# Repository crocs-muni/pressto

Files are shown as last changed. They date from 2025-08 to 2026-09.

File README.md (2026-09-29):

# PRESSTO
Physical Response Emulation System for Secure Testing Operations is a low-cost, fully automated, and reproducible hardware analysis platform. It enables precise and repeatable testing of devices by simulating human interaction such as button presses and screen reading without compromising cryptographic security assumptions.

**Known limits of v1** (observed on the hardware): at full reach an arm can bend, so the servo pushes the arm away instead of pressing the button; and v1 uses the SG90 in both of its versions, the 180° one and the continuous-rotation one, and the continuous-rotation servos are hard to calibrate.

<p align="center">
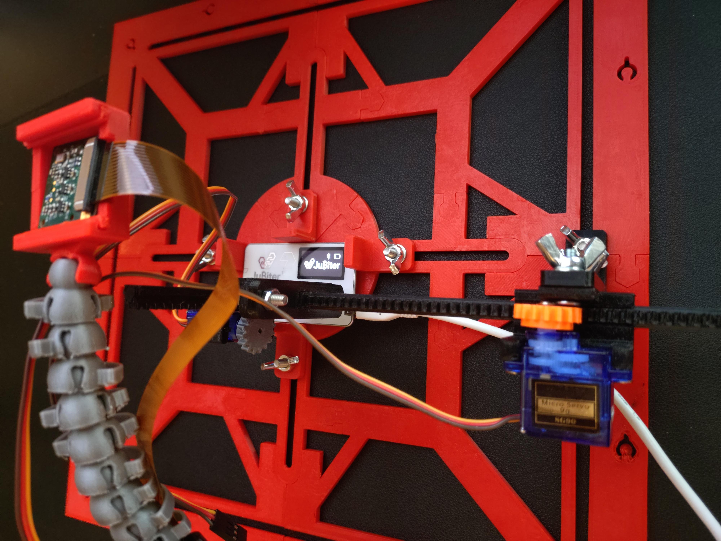
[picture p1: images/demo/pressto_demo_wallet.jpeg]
PRESSTO demo with a hardware wallet
  
  <br>
  <em>PRESSTO testing a hardware wallet</em>
</p>

## Features
- Automated physical interaction via Arduino-controlled servos
- OCR-based display capture

## Uses
- **Test physical inputs** – Consistently automate physical interaction like button presses or screen taps.  
- **Endurance testing** – Simulate hours or days of human interaction to reveal wear or intermittent faults.
- **Automated testing** – Fully automate operation of devices that can’t be driven purely by software, such as IoT appliances, hardware wallets etc.

## Where PRESSTO has been used

PRESSTO v1 was used for the study below, a large-scale security analysis of hardware wallets; so far it is PRESSTO's only published use, and this section will list further uses as they come. To cite PRESSTO, please cite this paper; its BibTeX entry follows.

[Large-Scale Security Analysis of Hardware Wallets](https://link.springer.com/chapter/10.1007/978-3-032-00633-2_21)

```bibtex
@inbook{Sorf_2025,
  title={Large-Scale Security Analysis of Hardware Wallets},
  ISBN={9783032006332},
  ISSN={1611-3349},
  url={http://dx.doi.org/10.1007/978-3-032-00633-2_21},
  DOI={10.1007/978-3-032-00633-2_21},
  booktitle={Availability, Reliability and Security},
  publisher={Springer Nature Switzerland},
  author={Šorf, Milan and Švenda, Petr and Chmielewski, Łukasz},
  year={2025},
  pages={360–377}
}
```

## Quickstart
Download the full set of models for one PRESSTO instance + printing instructions: [`quickstart.zip`](https://github.com/crocs-muni/pressto/releases/download/v1.0/quickstart.zip) (5.7 MB). The print list is also in [`stl/print.txt`](stl/print.txt).

## Bill of Materials (BOM)

This project requires a combination of 3D-printed parts, electronics, and standard mechanical fasteners. Below is the complete list of components:

### Mechanical Components

| Part | Description | DIN Spec | Quantity |
|---|---|---|---|
| M4 Hex Nuts | Standard M4 nuts for fastening | DIN 934 | Variable |
| M4 Machine Screws | M4 × 16 mm flat-head screws | DIN 965 | Variable |
| M4 Wing Nuts | Tool-free tightening, used for adjustable parts | DIN 315 | Variable |
| M4 Washers | Standard washers for load distribution | DIN 125A | Variable |

> Most joints can be assembled using a mix of these fasteners. Quantities depend on your specific configuration (number of arms, modules, etc.).

### 3D-Printed Parts

- STL files are provided in the [`stl/`](stl/) directory for immediate use.
- Original Autodesk Inventor (`.ipt`) files are also included in the [`ipt/`](ipt/) directory, allowing for easy customization and adaptation to your specific hardware or setup needs.
- Recommended print settings:
  - Material: PLA or PETG
  - Layer Height: 0.15 mm
  - Infill: 15–30% for strength
  - Supports: As needed per part
- The largest parts, measured in their STL files: `base_outer`, about 146 × 158 mm and 4 mm thick, and the racks, up to 165 mm long.

### Electronics

| Component | Notes | Quantity |
|---|---|---|
| Arduino Uno (or compatible) | For controlling servos | 1 |
| Raspberry Pi (any model with camera support) | For running OCR, camera capture, and automation scripts | 1 |
| SG90 Micro Servos | 2 per arm (e.g., one for press, one for movement) | ≥ 2 |
| Raspberry Pi Camera or USB Webcam | Used for OCR display capture | 1 |
| Power Supply | Depending on servo load | 1 |
| Display, keyboard and mouse (or remote access) | For the Raspberry Pi | — |
| USB cable | From the Arduino to the Raspberry Pi | — |
| Raspberry Pi power supply | For the Raspberry Pi (the Power Supply above is for the servos) | — |
| microSD card | For the Raspberry Pi | — |
| Camera cable | From the camera to the Raspberry Pi | — |
| Jumper wires | For the servo signal, power and ground connections | — |
| Breadboard | For the servo power and the common ground | — |
| Stylus tip (optional) | For touchscreens, grounded through a Dupont wire | — |

> The Arduino plugs into the Raspberry Pi, which drives the operation.

> Which Raspberry Pi to use depends on the use case: whether the images are processed on the Pi in real time, or only collected and sent to a stronger machine. PRESSTO v1 was tested on the Raspberry Pi Zero, 3, 4 and 5.

> "SG90" servos from one batch can be different makes, whose body dimensions differ. The holders fit both makes we measured, but cheap clones may differ, so stick with one type of servo.

> You can use a camera like the [Raspberry Pi Camera Module](https://www.raspberrypi.com/products/camera-module-3/), [Arducam](https://blog.arducam.com/raspberry-pi-multiple-cameras/) or any USB webcam (no mount is provided for a USB webcam).

### Tools

- Screwdrivers
- A spanner
- Side cutters (for the servo horn)

## Assembly Instructions

<details>
<summary><strong>Base</strong></summary>

<br>

The <strong>base</strong> forms the main support structure of the setup. It consists of 8 interlocking 3D-printed parts that slot together like a puzzle to create a rigid square frame.

### Required Parts

- 4 × [`base_inner.stl`](stl/base/base_inner.stl)
- 4 × [`base_outer.stl`](stl/base/base_outer.stl)

### Assembly Steps

1. Arrange the 4 <strong>outer</strong> parts to form the perimeter of the square.
2. Position the 4 <strong>inner</strong> parts so they form a cross-bracing pattern.
3. Slot all pieces together using the integrated puzzle joints.
4. Ensure the central circular section interlocks firmly with no gaps.  
   - No screws or adhesives are required — the snap-fit design holds everything in place.

### Visual Reference

| Description | Image |
|---|---|
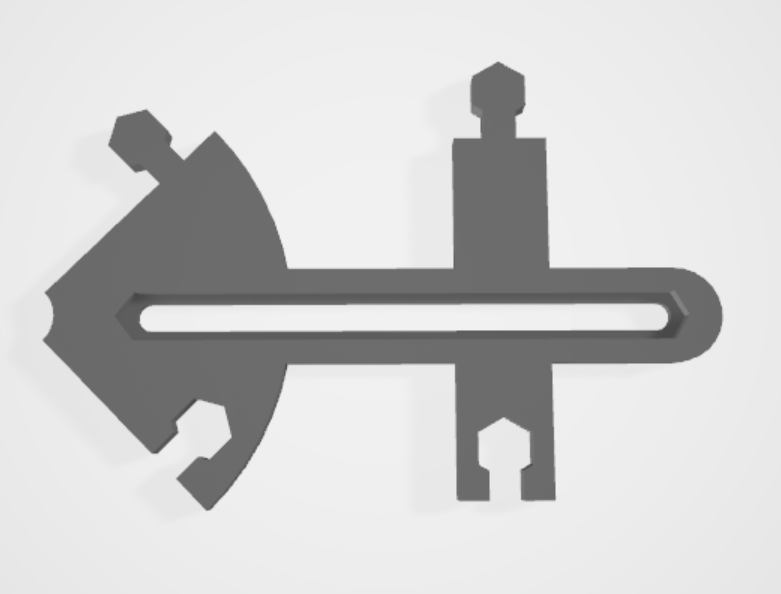
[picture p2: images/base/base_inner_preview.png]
STL preview of one inner base part
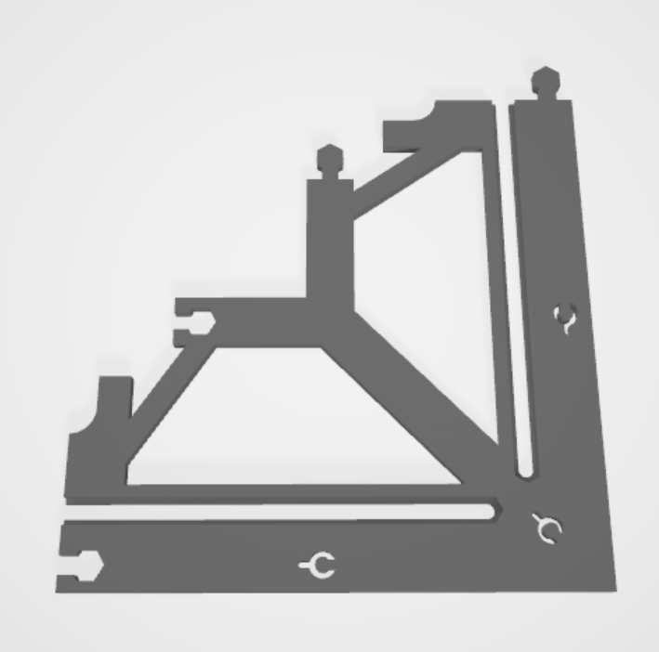
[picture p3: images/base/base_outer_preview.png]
STL preview of one outer base part
| Individual STL previews – `base_inner`, `base_outer` |   |
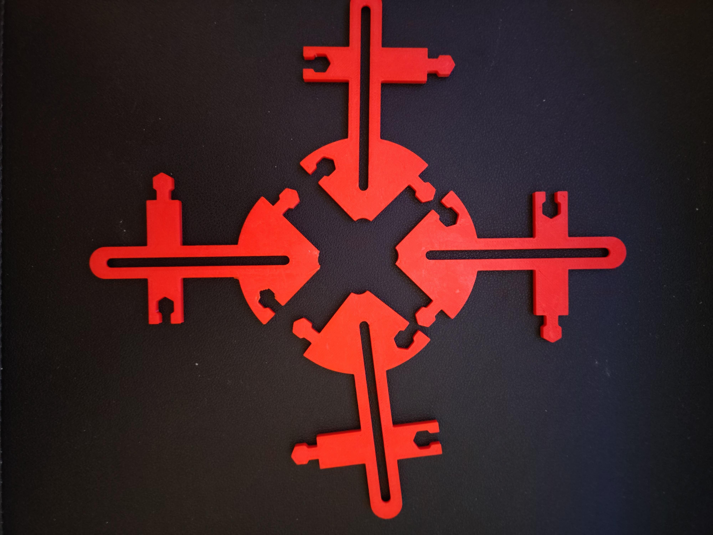
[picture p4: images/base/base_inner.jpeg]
Four printed inner base parts laid out in a cross
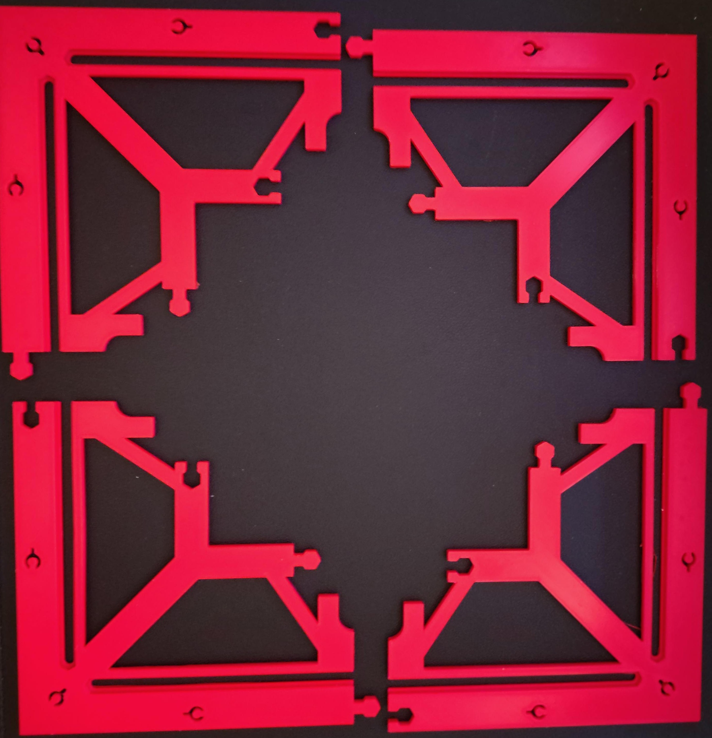
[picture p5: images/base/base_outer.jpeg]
Four printed outer base parts laid out as the corners of a square
| Printed individual pieces laid out |   |
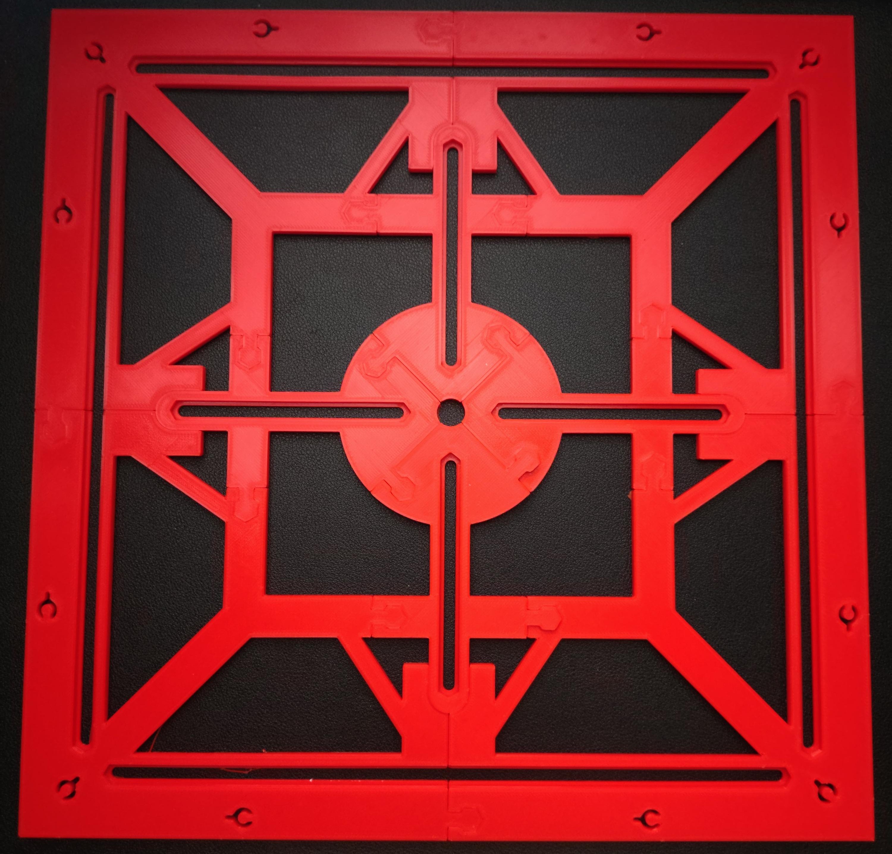
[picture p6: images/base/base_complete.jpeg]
Fully assembled square base seen from above
| Fully assembled base |  |

</details>

<details>
<summary><strong>Holder (Device Clamp)</strong></summary>

<br>

The <strong>holder</strong> secures the device in place using a simple mechanical clamp. It is fastened through the radial slots on the base and tightened manually using M4 hardware.

### Required Parts (per holder)

- 1 × [`holder.stl`](stl/holder/holder.stl)
- 1 × M4 × 16 mm screw (DIN 965)
- 1 × M4 washer (DIN 125A)
- 1 × M4 wing nut (DIN 315)

### Assembly Steps

1. Insert the M4 screw <strong>from below</strong> through one of the radial slots in the base.
2. Place the 3D-printed holder part onto the protruding screw (on top of the base).
3. Add a washer on top of the holder.
4. Thread a wing nut onto the screw and hand-tighten it.
5. Adjust the position of the holder as needed so it presses against the edge of your device.
6. Tighten the wing nut to lock the holder in place.

The M4 screw heads sit in a slot under the base, so the base does not rock.

### Visual Reference

| Description | Image |
|---|---|
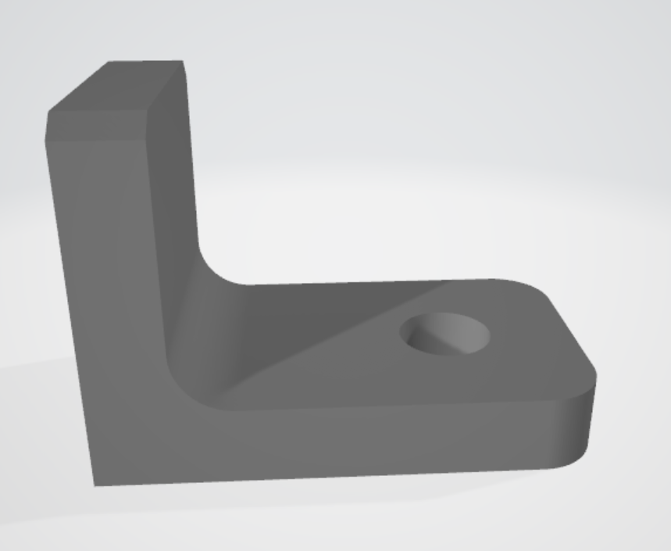
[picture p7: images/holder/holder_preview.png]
STL preview of the L-shaped holder with its screw hole
| STL preview – `holder` |  |
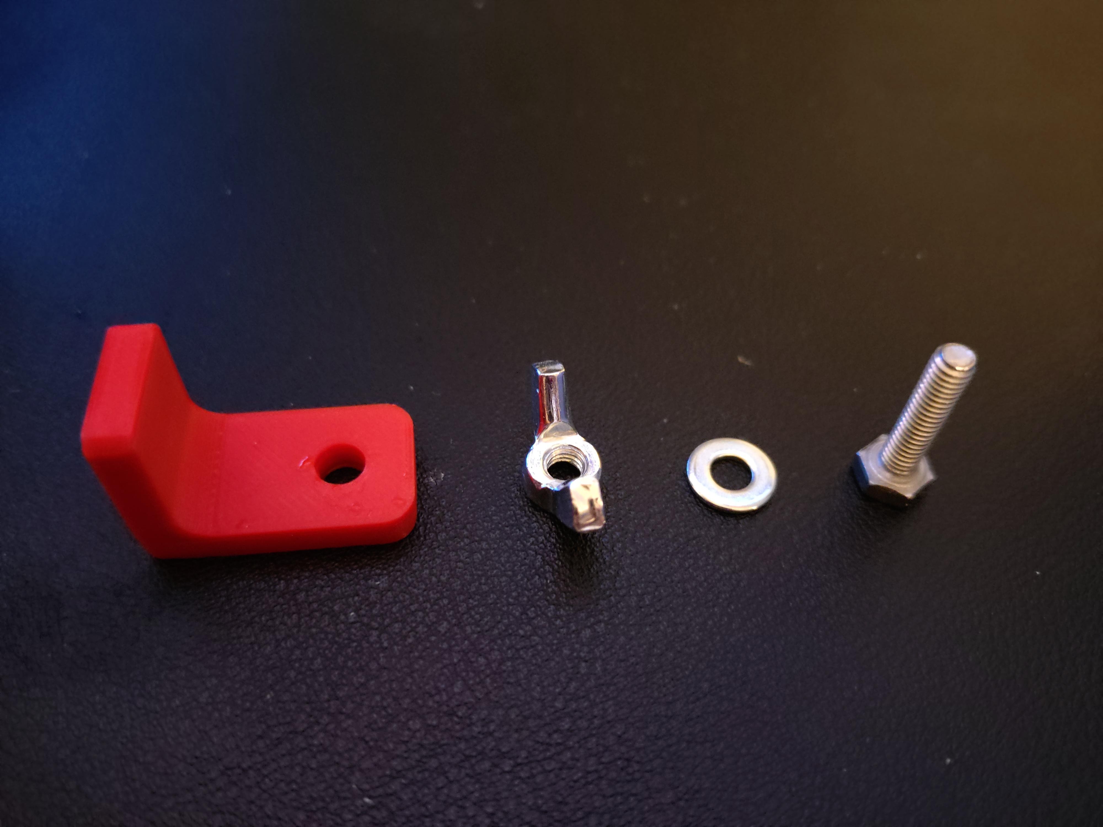
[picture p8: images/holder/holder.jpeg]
Printed holder next to a wing nut, a washer and a screw
| Hardware + printed holder |  |
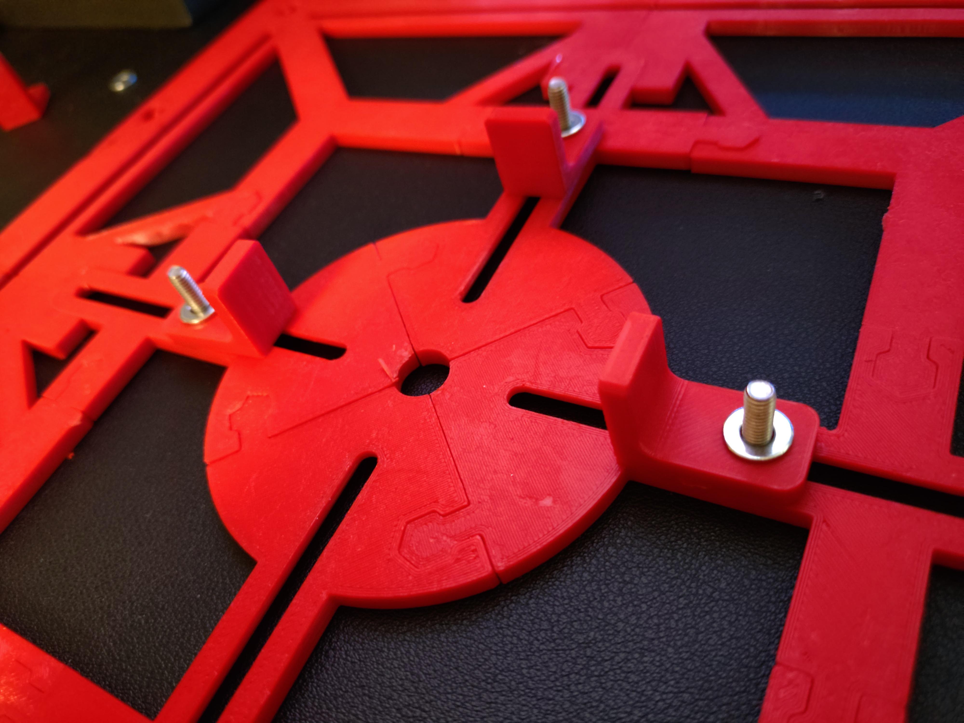
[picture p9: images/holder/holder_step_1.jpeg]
Three holders mounted on the base with screws and washers
| Mounted holders |  |
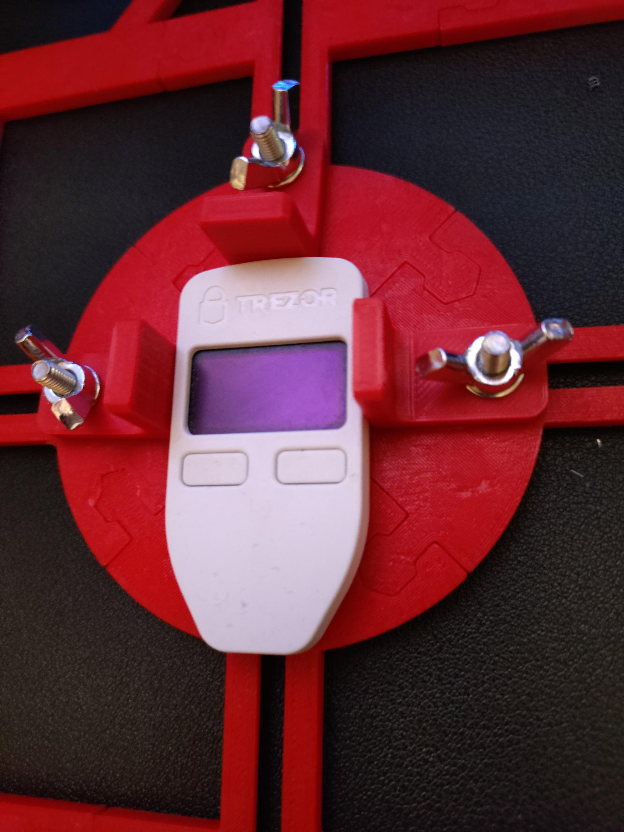
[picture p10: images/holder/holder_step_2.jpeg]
Three holders with wing nuts clamping a hardware wallet on the base
| Holders with a device |  |

</details>

<details>
<summary><strong>Camera Arm</strong></summary>

<br>

The <strong>camera arm</strong> consists of three main components:
1. <strong>Arm Base</strong> – fits into the outer slots of the main base, no fasteners required.
2. <strong>Ball Joints</strong> – form the adjustable arm; hollow and designed with side hooks for cable management or threading smaller cables inside.
3. <strong>Camera Holder</strong> – attaches to the last ball joint to securely hold the camera; it fits the Raspberry Pi camera modules and Arducam cameras, which share one board format.

### Required Parts

- 1 × [`arm_base.stl`](stl/camera_arm/arm_base.stl)
- Multiple × [`ball_joint.stl`](stl/camera_arm/ball_joint.stl) (depending on desired arm length)
- 1 × [`camera_holder.stl`](stl/camera_arm/camera_holder.stl)

### Assembly Steps

1. Insert the <strong>arm base</strong> into one of the outer slots of the main base: its keyed stem goes into one of the round keyhole sockets of the outer parts (three in each `base_outer`), not into one of the slots for M4 screws (those take the screws of the device holders and of the stand).
2. Connect <strong>ball joints</strong> together until you reach the desired arm length.  
   - Ball joints can be rotated to adjust the arm angle.  
   - Use the built-in hooks or hollow core for cable routing.
3. Attach the <strong>camera holder</strong> to the last ball joint.
4. Mount the camera into the holder.
5. Adjust the arm’s position and angles as needed for optimal camera view.

### Visual Reference

| Description | Image |
|---|---|
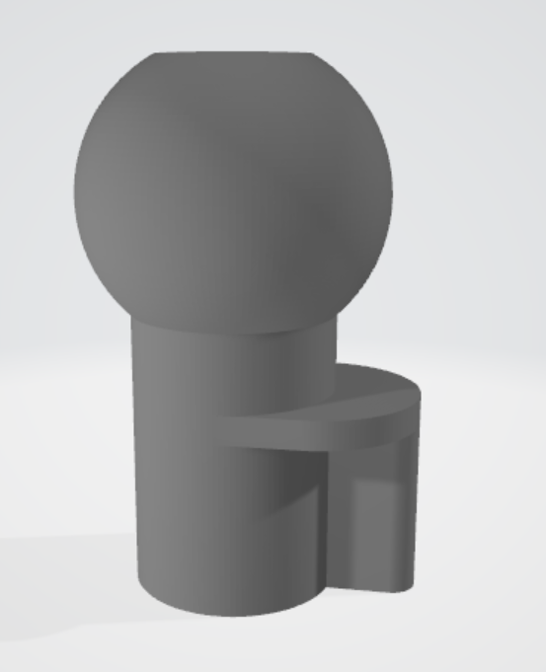
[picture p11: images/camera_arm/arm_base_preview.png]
STL preview of the arm base with its ball end
| STL preview – `arm_base` |  |
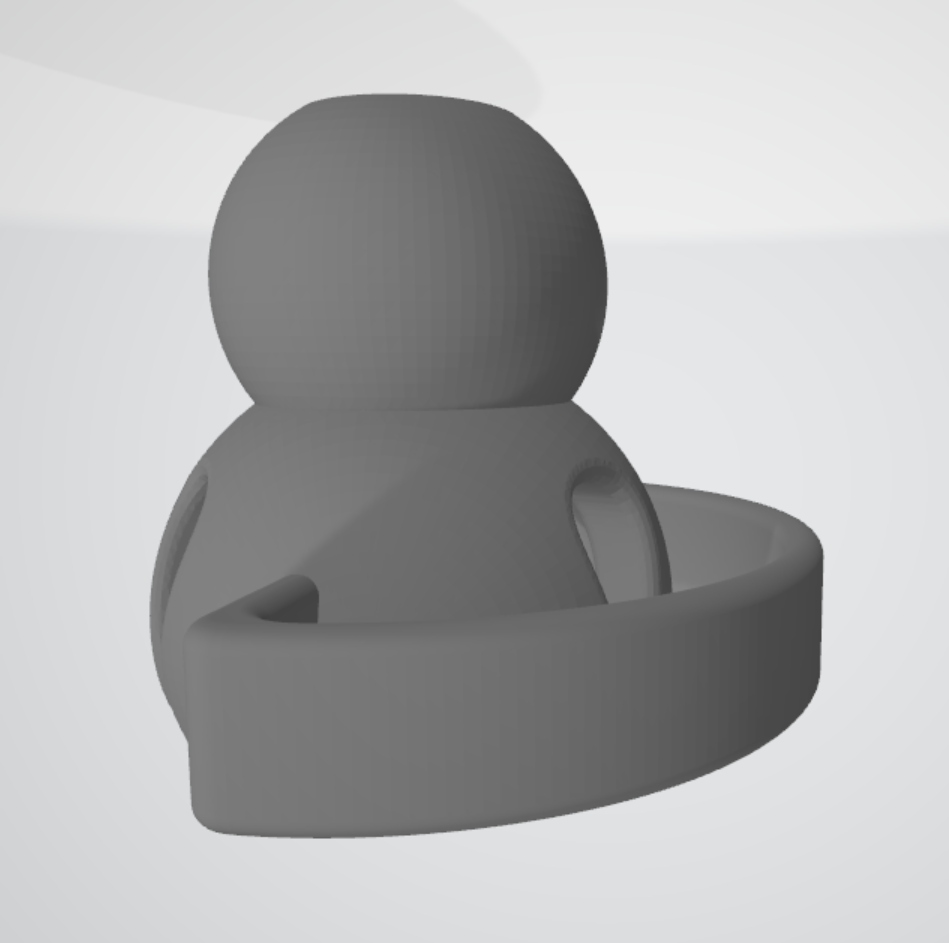
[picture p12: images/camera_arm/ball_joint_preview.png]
STL preview of a ball joint with its side hook
| STL preview – `ball_joint` |  |
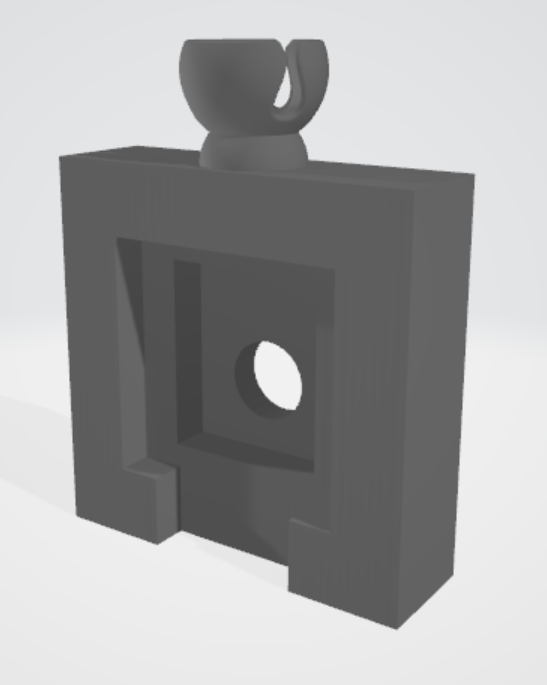
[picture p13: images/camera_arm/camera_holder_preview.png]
STL preview of the camera holder with its lens opening
| STL preview – `camera_holder` |  |
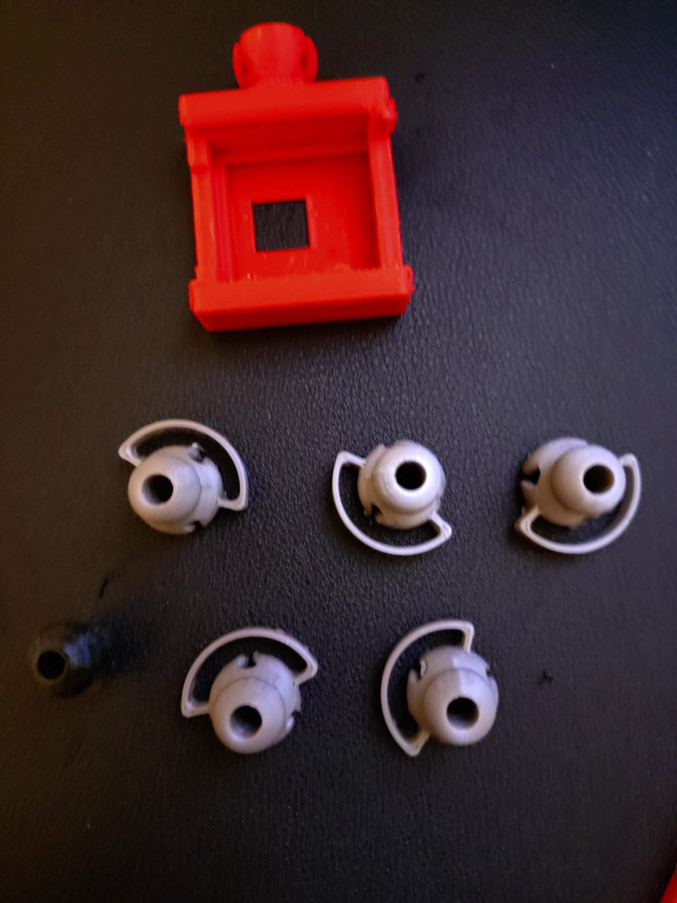
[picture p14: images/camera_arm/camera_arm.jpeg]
Printed camera holder above five printed ball joints
| Printed camera arm components |  |
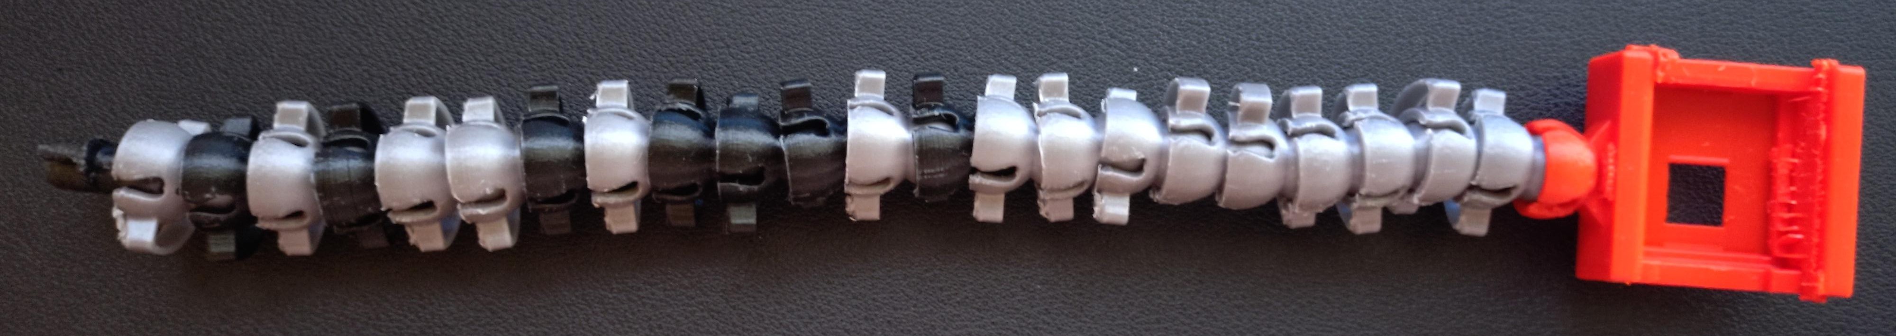
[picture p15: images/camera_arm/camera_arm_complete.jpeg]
Assembled camera arm, a chain of ball joints ending in the camera holder
| Fully assembled camera arm |  |

The photos show an earlier print with a square lens opening; the published CAD has a round one. Both fit, and the CAD is the reference.

</details>

<details>
<summary><strong>Actuator Arm – Pinion Gear</strong></summary>

<br>

The <strong>pinion gear</strong> connects to the SG90 servo’s output shaft through the hub of a cut-down servo horn. It is used to transfer rotational motion from the servo to other moving parts in the actuator assembly.

A full arm uses two pinions: one for the press, one for moving the pressing part back and forth.

The pinion caps over the hub of a stock SG90 horn cut free of its arms; the horn screw clamps it through the pinion's centre hole.

### Required Parts

- 1 × [`pinion_gear.stl`](stl/pinion_gear/pinion_gear.stl)
- 1 × SG90 servo motor
- 1 × stock SG90 horn, cut free of its arms (only its hub is used)
- 1 × Servo mounting screw (comes with SG90)

### Assembly Steps

1. Cap the printed <strong>pinion gear</strong> over the hub of a cut-down SG90 horn (the hub goes into the round socket in one face of the pinion; that face points to the servo), and seat the hub on the output shaft of the SG90 servo.
2. Align the gear so that it sits flush against the servo horn mount.
3. Secure the gear using the small screw provided with the SG90 servo.

### Visual Reference

| Description | Image |
|---|---|
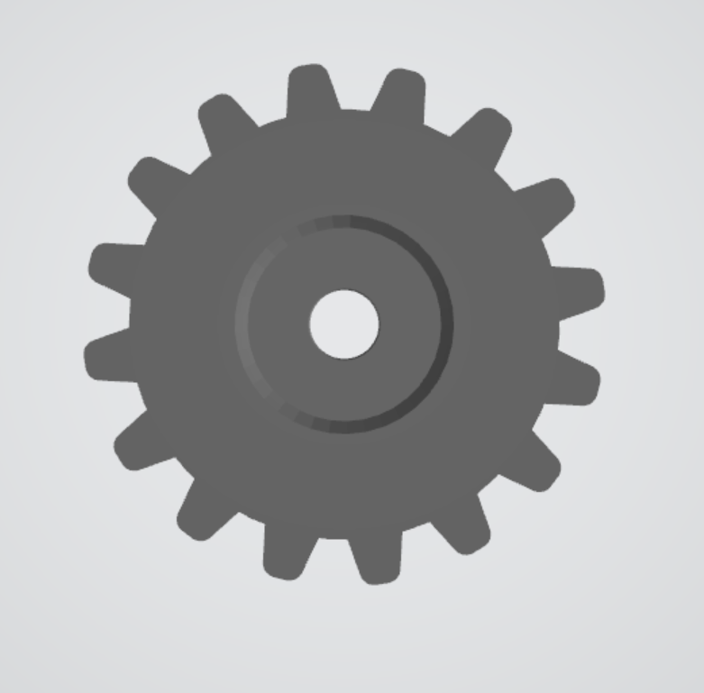
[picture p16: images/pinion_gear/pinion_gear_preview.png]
STL preview of the pinion gear seen face-on
| STL preview – `pinion_gear` |  |
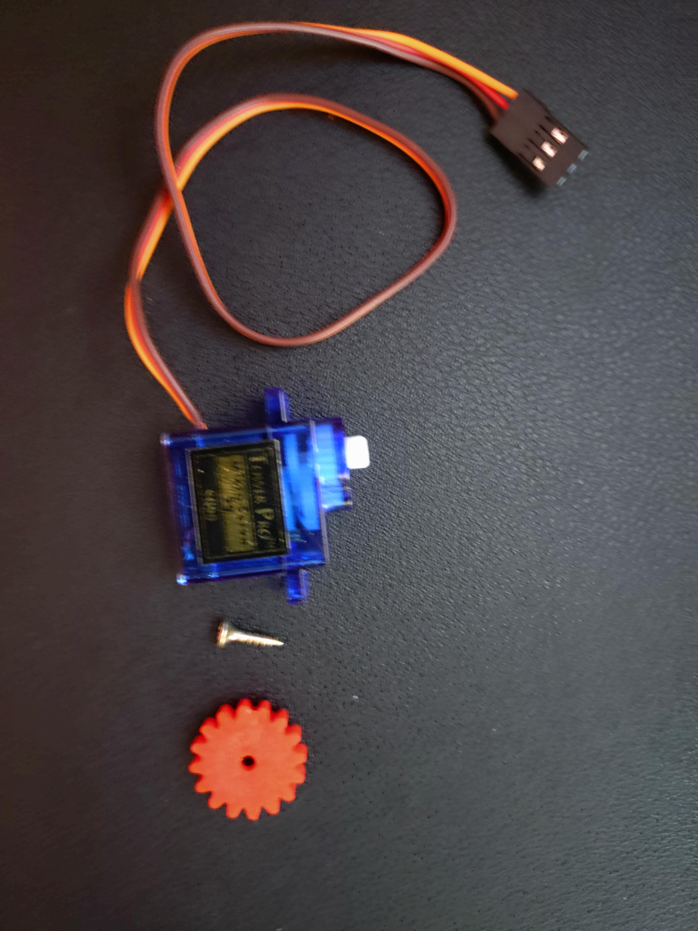
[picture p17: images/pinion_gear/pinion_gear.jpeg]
Printed pinion gear, a small screw and an SG90 servo with its cable
| Printed gear + SG90 servo |  |

</details>

<details>
<summary><strong>Actuator Arm Base</strong></summary>

<br>

The Actuator Arm Base moves the actuator over the device and retracts it to give the camera an unobstructed view.

### Required Parts

- 1 × [`pinion_gear.stl`](stl/pinion_gear/pinion_gear.stl) — attached to the SG90 servo output shaft through the hub of a cut-down horn  
- 1 × SG90 micro servo (with 2 × mounting screws supplied with the servo)  
- 1 × [`actuator_arm_base_motor_holder.stl`](stl/actuator_arm_base/actuator_arm_base_motor_holder.stl) <em>or</em>, for easier installation, [`actuator_arm_base_motor_holder_single_hole.stl`](stl/actuator_arm_base/actuator_arm_base_motor_holder_single_hole.stl) — to secure the servo  
- 1 × [`actuator_arm_base_rack.stl`](stl/actuator_arm_base/actuator_arm_base_rack.stl) <em>or</em> [`actuator_arm_base_rack_with_mount.stl`](stl/actuator_arm_base/actuator_arm_base_rack_with_mount.stl) — for linear motion  
- 1 × [`actuator_arm_base_stand.stl`](stl/actuator_arm_base/actuator_arm_base_stand.stl) — to mount the assembly to the base  
- 2 × M4 × 16 mm machine screws (DIN 965)  
- 2 × M4 washers (DIN 125A)  
- 2 × M4 wing nuts (DIN 315) — to attach motor holder to the stand  
- 1 × M4 × 16 mm machine screw (DIN 965)  
- 1 × M4 washer (DIN 125A)  
- 1 × M4 wing nut (DIN 315) — to mount the stand to the base

### Assembly Notes

- The SG90 servo is fixed into the <strong>motor holder</strong> using the two screws supplied with the SG90.  
- The <strong>stand</strong> mounts to the <strong>outer base slot</strong> in the same way as the device holder — using an M4 screw, washer, and wing nut from below.  
- The <strong>motor holder</strong> attaches to the stand at the desired height using two M4 screws, washers, and wing nuts.  
  - If space is tight (for example, with multiple arms close together), a regular M4 machine screw with a hex nut (DIN 934) may be used instead of the wing nut on one side.  
- For <strong>easier assembly</strong>, insert at least the inside M4 screw into the motor holder <strong>before</strong> inserting the rack — otherwise, it will be blocked.

**Recommended assembly sequence**  
1. Insert the inside M4 screw into the motor holder.  
2. Slide in the rack.  
3. Attach the SG90 servo with the pinion gear already mounted, using its supplied screws.  
4. Insert the remaining M4 screw.  
5. Attach the motor holder to the stand with the two M4 screws, washers, and wing nuts.  
6. Mount the stand to the base.

### Visual Reference

| Description | Image |
|---|---|
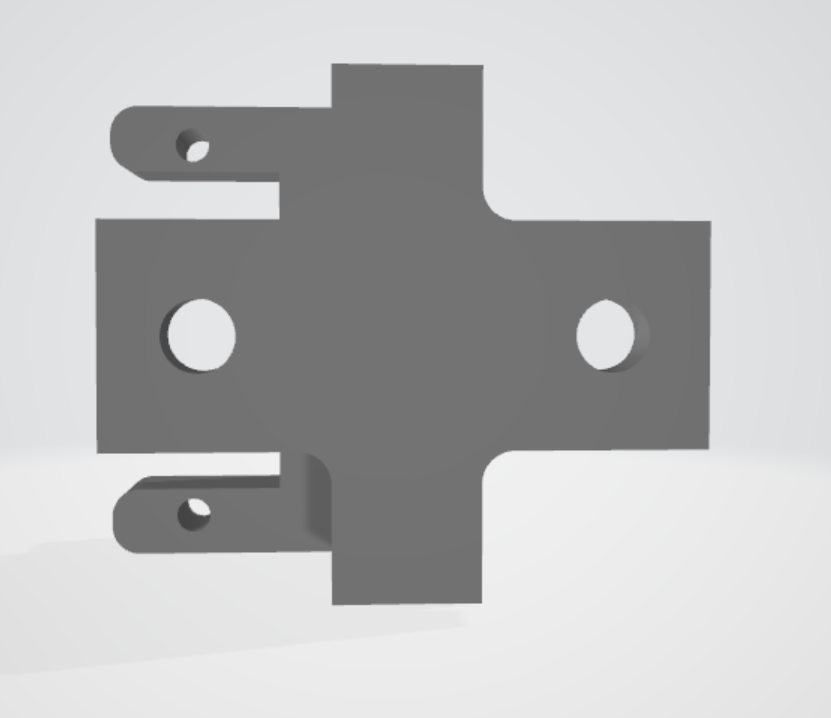
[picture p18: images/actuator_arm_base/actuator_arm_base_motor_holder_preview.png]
STL preview of the motor holder of the actuator arm base, with two large holes and two servo ears
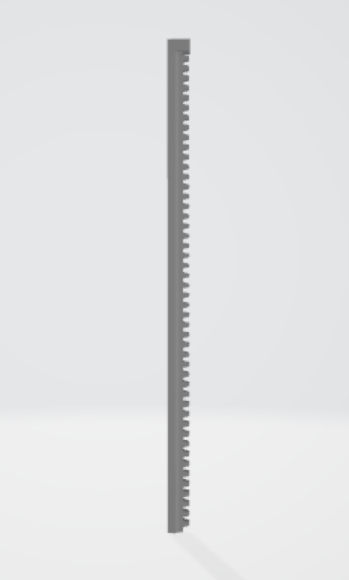
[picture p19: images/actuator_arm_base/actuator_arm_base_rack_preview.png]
STL preview of the base rack, a long toothed bar
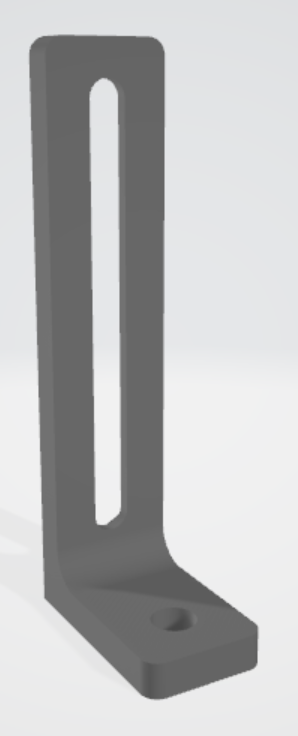
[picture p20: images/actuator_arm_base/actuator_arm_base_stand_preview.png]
STL preview of the stand, an L-shaped part with a long slot
| Individual STL previews – `actuator_arm_base_motor_holder`, `actuator_arm_base_rack`, `actuator_arm_base_stand` |    |
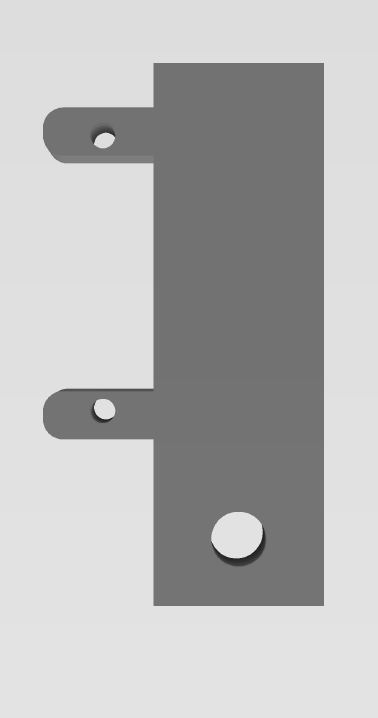
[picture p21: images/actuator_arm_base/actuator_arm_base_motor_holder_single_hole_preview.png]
STL preview of the single-hole motor holder of the actuator arm base, with one large hole and two servo ears
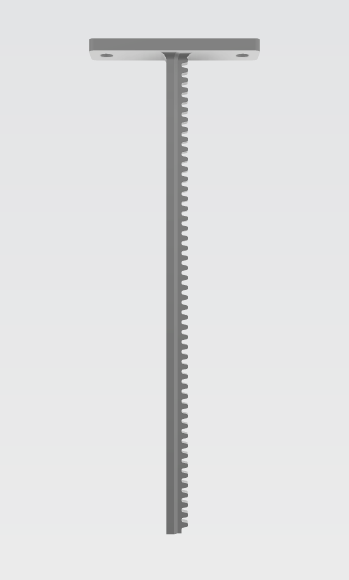
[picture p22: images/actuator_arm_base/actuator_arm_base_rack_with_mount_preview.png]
STL preview of the base rack with mount, a long toothed bar with a flat two-hole plate at one end
| Individual STL previews – `actuator_arm_base_motor_holder_single_hole`, `actuator_arm_base_rack_with_mount` |   |
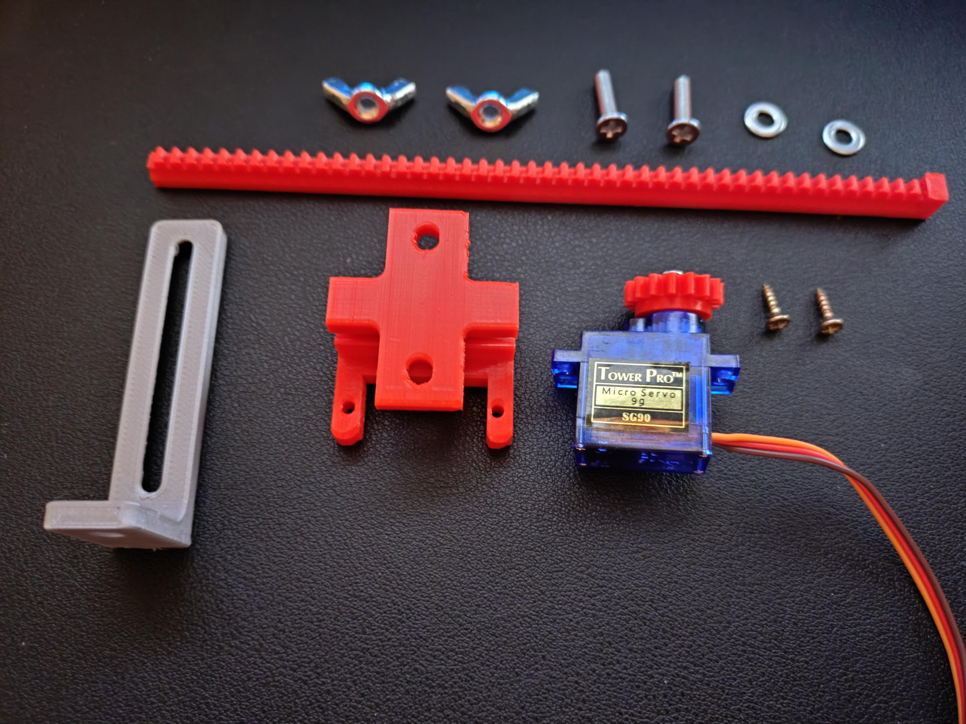
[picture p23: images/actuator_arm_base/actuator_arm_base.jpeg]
Parts of the actuator arm base laid out: rack, stand, motor holder, SG90 servo with pinion gear, screws, washers and wing nuts
| SG90 with attached `pinion_gear` and motor holder parts |  |
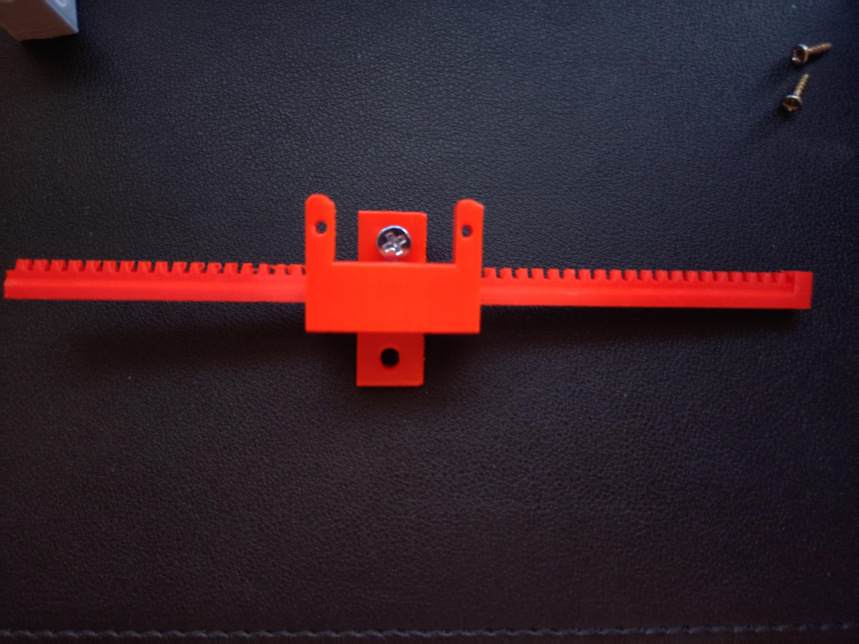
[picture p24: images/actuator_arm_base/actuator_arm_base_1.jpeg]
Rack slid through the motor holder with one M4 screw in place, servo not yet attached
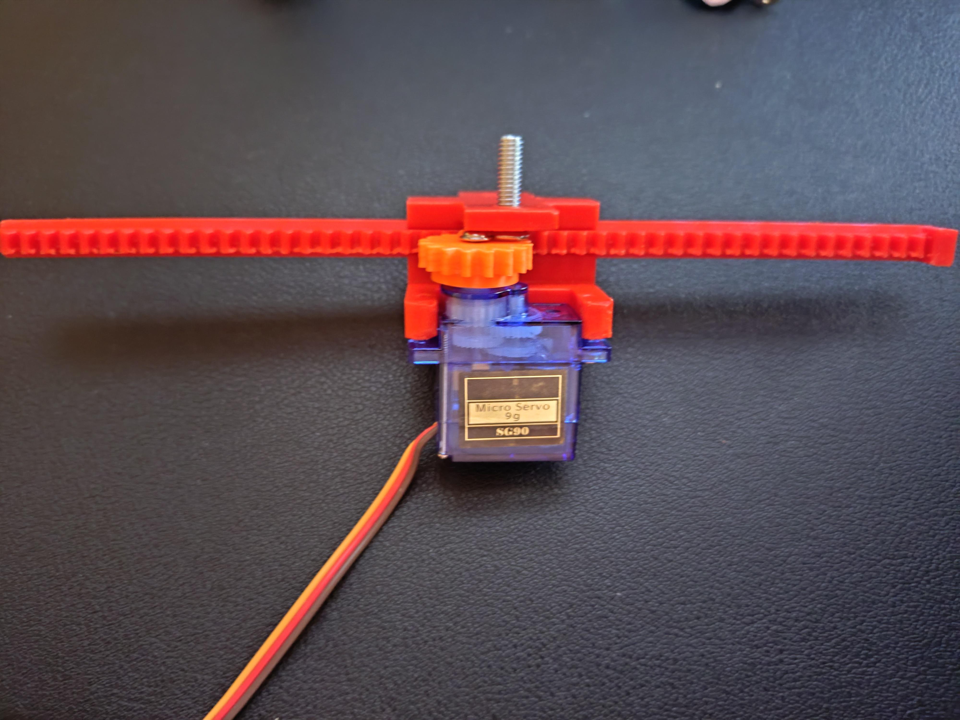
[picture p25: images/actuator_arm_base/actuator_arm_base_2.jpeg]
SG90 servo with pinion gear attached to the motor holder, the gear meshing with the rack
| Partially assembled: rack in place, then servo added |   |
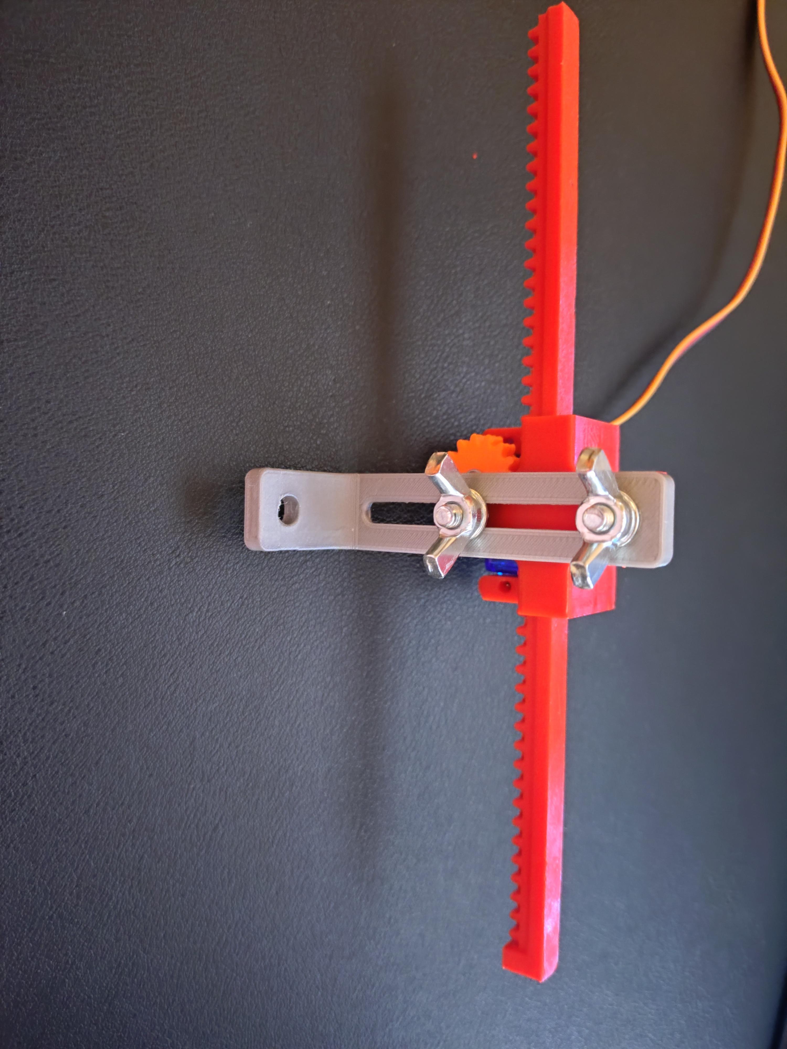
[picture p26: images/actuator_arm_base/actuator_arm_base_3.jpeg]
Motor holder with servo and rack fastened to the stand with two wing nuts
| Mounted on stand, ready to attach to base |  |

</details>

<details>
<summary><strong>Actuator Arm</strong></summary>

<br>

The actuator arm is the moving element that pushes buttons or touches a screen.  
It connects directly to the [`actuator_arm_base_rack.stl`](stl/actuator_arm_base/actuator_arm_base_rack.stl) and is driven by an SG90 servo with the [`pinion_gear.stl`](stl/pinion_gear/pinion_gear.stl) attached.

### Required Parts

- 1 × [`pinion_gear.stl`](stl/pinion_gear/pinion_gear.stl) — attached to the SG90 servo output shaft through the hub of a cut-down horn  
- 1 × SG90 micro servo (with 2 × mounting screws supplied with the servo)  
- 1 × [`actuator_arm_motor_holder_mount.stl`](stl/actuator_arm/actuator_arm_motor_holder_mount.stl) — bracket, bolted to the motor holder; the base rack slides into its square mount hole  
- 1 × [`actuator_arm_rack.stl`](stl/actuator_arm/actuator_arm_rack.stl) <em>or</em> [`actuator_arm_rack_wide.stl`](stl/actuator_arm/actuator_arm_rack_wide.stl) — for linear motion; different shapes, for easier access to different buttons  
- 1 × [`actuator_arm_motor_holder.stl`](stl/actuator_arm/actuator_arm_motor_holder.stl) — attaches to the rack and connects to the base  
- 2 × M4 × 16 mm machine screws (DIN 965)  
- 2 × M4 washers (DIN 125A)  
- 2 × M4 hex nuts (DIN 934) — to attach the motor holder to the mount  
- Optional: stylus tip for touchscreens, grounded through a Dupont wire

### Assembly Steps

1. <strong>Attach the bracket</strong> ([`actuator_arm_motor_holder_mount.stl`](stl/actuator_arm/actuator_arm_motor_holder_mount.stl)) to the motor holder using 2 × M4 machine screws with washers and hex nuts.
2. <strong>Insert the rack</strong> ([`actuator_arm_rack.stl`](stl/actuator_arm/actuator_arm_rack.stl) or [`actuator_arm_rack_wide.stl`](stl/actuator_arm/actuator_arm_rack_wide.stl)) into the motor holder.
3. <strong>Install the SG90 servo</strong>: attach the [`pinion_gear.stl`](stl/pinion_gear/pinion_gear.stl) to the servo output shaft through the hub of a cut-down horn, align with the rack teeth, and fasten the servo using the 2 screws supplied with the SG90.

### Visual Reference

| Description | Image |
|---|---|
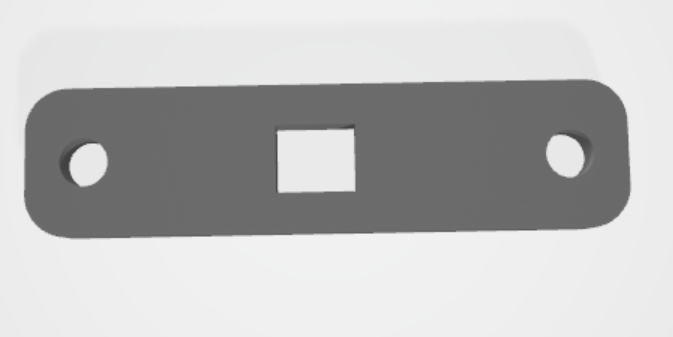
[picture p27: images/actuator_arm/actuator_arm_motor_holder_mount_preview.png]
STL preview of the bracket, a flat plate with a square opening between two round holes
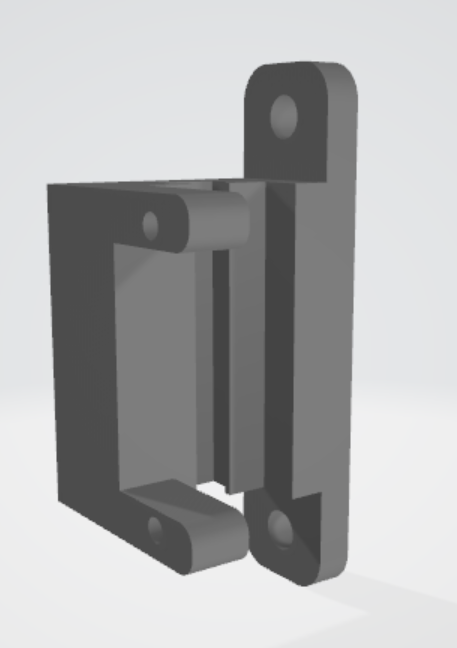
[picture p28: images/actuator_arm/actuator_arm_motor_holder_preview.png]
STL preview of the motor holder of the actuator arm, with two small ears and a two-hole flange
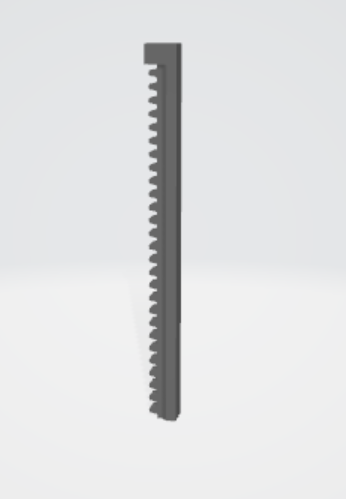
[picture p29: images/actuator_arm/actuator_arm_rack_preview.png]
STL preview of the actuator arm rack, a toothed bar with a short head
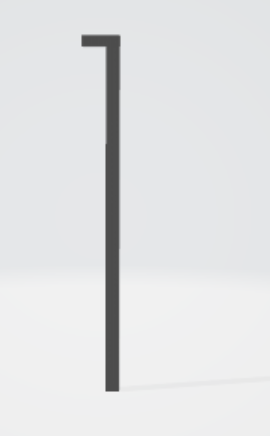
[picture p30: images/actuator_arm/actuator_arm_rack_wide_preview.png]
STL preview of the alternative actuator arm rack seen edge-on, with an L-shaped head
| Individual STL previews – `actuator_arm_motor_holder_mount`, `actuator_arm_motor_holder`, `actuator_arm_rack`, `actuator_arm_rack_wide` |     |
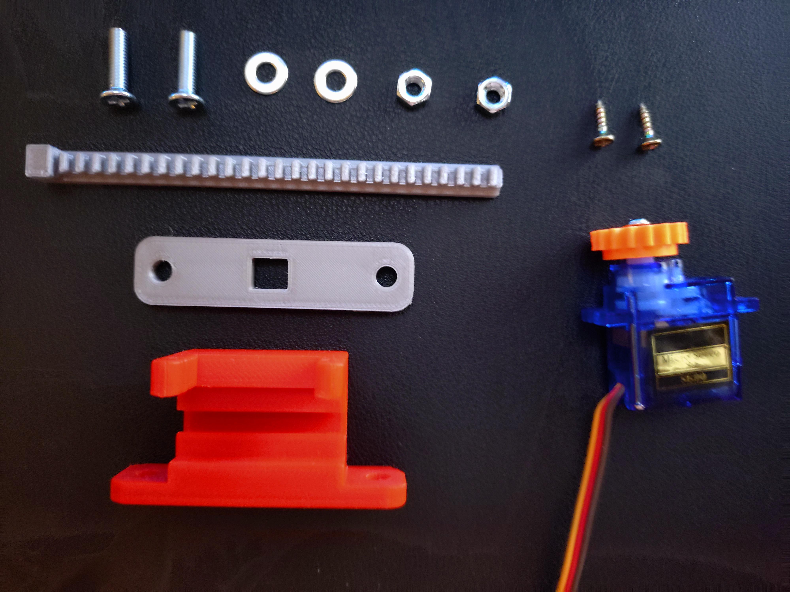
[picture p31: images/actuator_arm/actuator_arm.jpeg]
Parts of the actuator arm laid out: rack, bracket, motor holder, SG90 servo with pinion gear, screws, washers and hex nuts
| Actuator arm assembly |  |
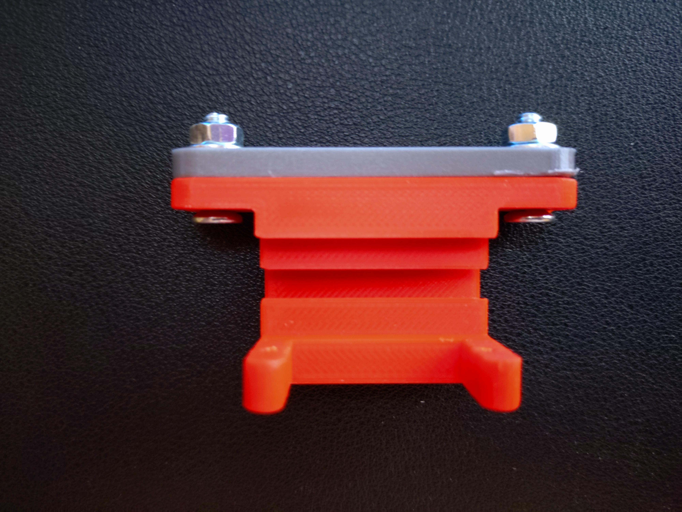
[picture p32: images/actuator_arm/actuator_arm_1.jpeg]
Bracket bolted to the motor holder with two screws and hex nuts
| Bracket bolted to the motor holder |  |
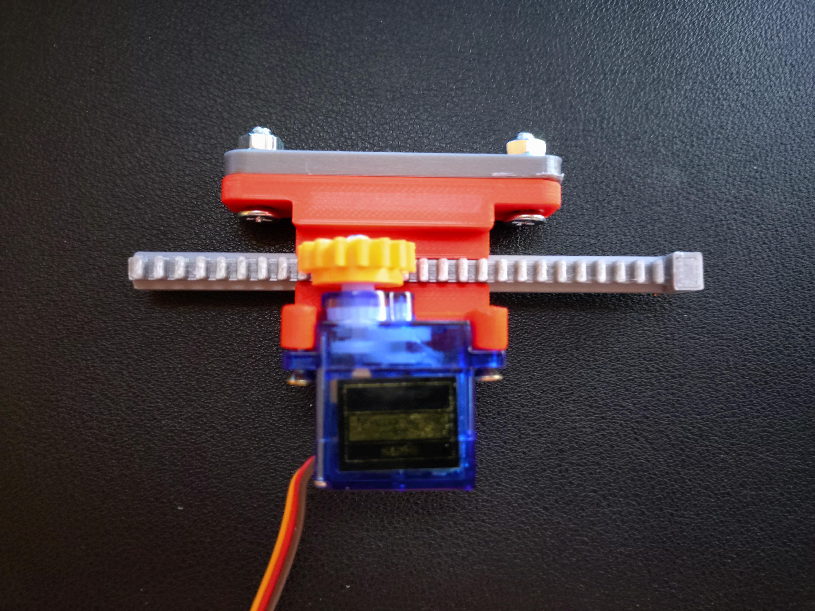
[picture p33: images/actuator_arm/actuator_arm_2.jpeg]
Actuator arm with the rack inserted and the servo installed, its pinion gear meshing with the rack
| Mounted actuator arm |  |

### Connecting the Actuator Arm to the Base

No screws are needed for this step – simply slide the [`actuator_arm_base_rack.stl`](stl/actuator_arm_base/actuator_arm_base_rack.stl) into the square mount hole in the middle of the [`actuator_arm_motor_holder_mount.stl`](stl/actuator_arm/actuator_arm_motor_holder_mount.stl) plate until it seats fully.

| Step | Image |
|---|---|
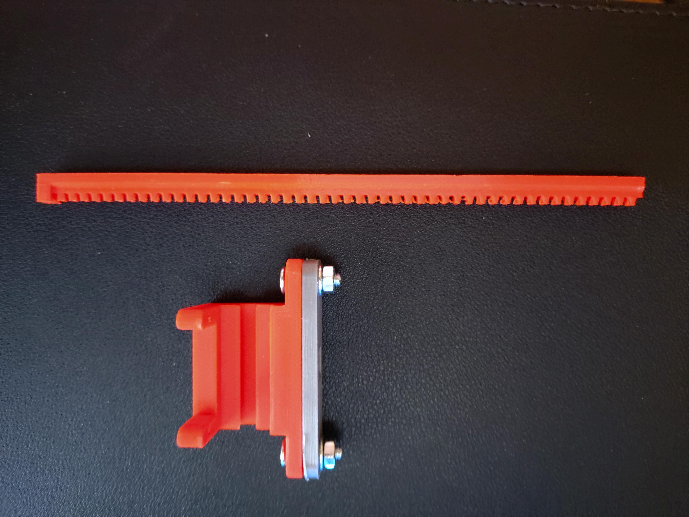
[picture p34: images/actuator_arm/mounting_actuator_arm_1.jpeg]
Base rack lying next to the motor holder and bracket before it is inserted
| Align the base rack with the actuator arm mount hole |  |
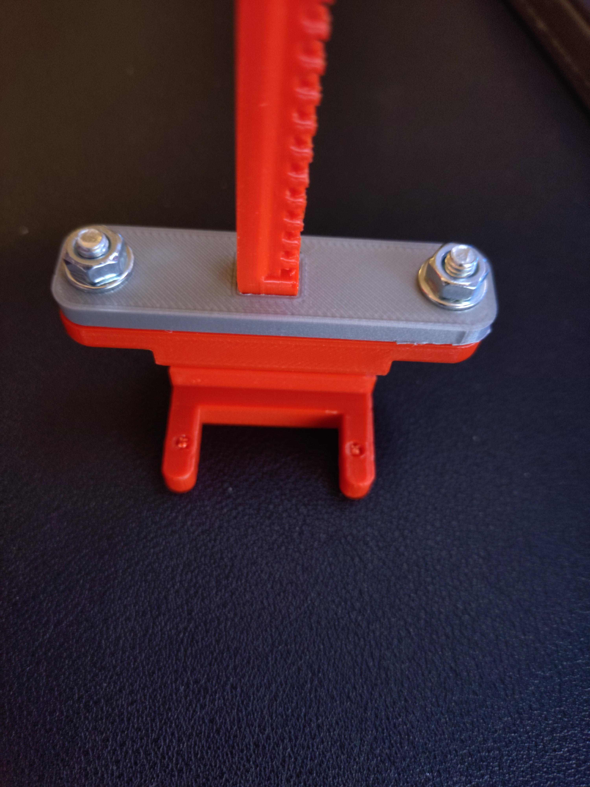
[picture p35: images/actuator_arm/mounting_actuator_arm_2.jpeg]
Base rack seated in the mount hole of the actuator arm
| Slide until seated fully |  |

</details>

## Software / demos

The [`demos/`](demos/) directory holds the example code. The table repeats what each file says about itself in its header or docstring and lists its third-party includes and imports.

| File | Purpose | Third-party imports | Hardware | How to run |
|---|---|---|---|---|
| [`servos.ino`](demos/servos.ino) | Demo file for 2 servo arms to press buttons | `#include`: `Servo.h` | Arduino | Flash it to an Arduino |
| [`servos.py`](demos/servos.py) | Demo of Arduino servo pressing via USB serial | `serial` | Arduino on USB serial | From another script: `from servos import press_left, press_right, press_both`; optionally `set_port("/dev/ttyACM0")` to pin the port if autodetect guesses wrong |
| [`pca_servos.py`](demos/pca_servos.py) | PCA9685 servo pressing via I2C | `board`, `busio`, `adafruit_pca9685` | Raspberry Pi, PCA9685 | From another script: `from pca_servos import press_left, press_right, press_both`; the docstring also lists optional tuning calls |
| [`ocr_demo.py`](demos/ocr_demo.py) | Demo file for OCR and possible preprocessing | `pytesseract`, `PIL`, `cv2`, `numpy`, `matplotlib` | Raspberry Pi | Run it on a Raspberry Pi |
| [`cars/`](demos/cars/) | The cars demo: PRESSTO plays a two-cars phone game (a camera watches the phone, two servo arms tap it) | `cv2`, `numpy`, `board`, `busio`, `adafruit_pca9685`, `gpiozero`, `picamera2`, `libcamera` | Raspberry Pi with a display, a camera and a PCA9685; a phone running the game | Camera check, `calibrate.py`, then `cars_pca.py`: see [`demos/cars/README.md`](demos/cars/README.md) |

Both Python servo files end with a small command-line test: `python3 demos/servos.py --left` (also `--right`, `--both`, and `--port /dev/ttyACM0` to pick the serial port) and `python3 demos/pca_servos.py --both` (also `--left`, `--right`).

`ocr_demo.py` is a short demo: run it on the Raspberry Pi with `python3 demos/ocr_demo.py`. It needs a display, because it shows the processed image (`plt.show()`) before it prints the detected text, and it calls `rpicam-still` to capture the image.

The docstring of `pca_servos.py` carries two notes, quoted here verbatim:

> - Requires external 5V on PCA V+ for servos.
> - Pi GND must be common with PCA GND.

Future versions are planned to replace the Arduino with a servo driver board on the Raspberry Pi's I²C bus; `demos/pca_servos.py` already drives the servos that way (PCA9685).

### Serial protocol of `servos.ino`

The sketch opens the serial port at `115200` baud and prints `READY` once it has started. It then reads one command per line: a command ends with a newline, and the input is trimmed and converted to upper case before it is compared.

| Command | Action | Reply |
|---|---|---|
| `P0` | press left (index 0) | `OK P0` |
| `P1` | press right (index 1) | `OK P1` |
| `PA` | press both simultaneously | `OK PA` |

Any other non-empty line is answered with `ERR (use P0, P1, or PA)`.

Servo signal pins: `9` (left) and `10` (right).

The servos need their own 5 V supply — a lab supply or a standard smartphone charger (through a USB breakout board) both do the job; do not power them from the Arduino's 5 V pin. Connect the supply's ground to the Arduino's GND.

`servos.py` is the Python side of this protocol; its docstring notes that `press_both()` needs a sketch that supports `PA`.

### Installing the dependencies

The Python packages that the demos import are listed, by their PyPI project names, in [`demos/requirements.txt`](demos/requirements.txt); the comments in that file say which demo imports what. From the root of the repository:

```
python3 -m pip install -r demos/requirements.txt
```

The cars demo lists its packages in `demos/cars/requirements.txt` and its install notes in `demos/cars/README.md`.

From Raspberry Pi OS Bookworm onwards, pip installs only into a Python virtual environment: create one with `python3 -m venv env`, enter it with `source env/bin/activate`, then run the pip line.

`pytesseract` is a wrapper for Google's Tesseract OCR engine. The engine is a separate program that pip does not install: install it on its own, so that the `tesseract` command can be invoked.

`servos.ino` includes the Arduino `Servo` library. The sketch says where to get it:

> in Arduino IDE: Tools -> Manage Libraries... -> search "Servo" -> install

## License

The MIT licence in [`LICENSE`](LICENSE) covers every file in this repository, including the CAD (`.ipt`) and STL files.

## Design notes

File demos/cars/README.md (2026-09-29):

# Cars demo: PRESSTO plays a phone game

https://github.com/user-attachments/assets/829fcdeb-2ff4-44f2-bf4d-515deed96533

*PRESSTO playing the cars game: two servo arms tap a phone clamped in the base. The video is also attached to the [PRESSTO `v1.0` release](https://github.com/crocs-muni/pressto/releases/tag/v1.0).*

PRESSTO plays a two-cars phone game: a camera watches the phone's screen and two servo arms tap it. The game shows two cars in four lanes (0 to 3, from the left), with green circles to collect and red squares to avoid. A tap on the left half of the screen switches the left car between lanes 0 and 1, a tap on the right half switches the right car between lanes 2 and 3; the left arm taps the left half, the right arm the right half. The bot taps to move a car away from an object to avoid in its lane, or towards an object to collect in its other lane.

The game is an Android app written for this demo, in its own repository: [pressto-cars-game](https://github.com/crocs-muni/pressto-cars-game).

Three programs run on the Raspberry Pi, in this order:

| Program | What it does |
|---|---|
| [`test_camera.py`](test_camera.py) | camera check: finds the camera, reads frames, saves the last one; opens no window |
| [`calibrate.py`](calibrate.py) | calibration: marks the game area and samples the colours; writes `calibration.json` |
| [`cars_pca.py`](cars_pca.py) | the bot: reads `calibration.json`, watches the game and taps |

## What you need

- A Raspberry Pi running Raspberry Pi OS with its desktop, **a display, a keyboard and a mouse**. `calibrate.py` and `cars_pca.py` show OpenCV windows and read the keyboard (and, in `calibrate.py`, the mouse) through them; there is no headless mode yet.
- A camera that sees the whole phone screen: a Raspberry Pi camera through Picamera2, or a USB camera through OpenCV (device 0). The programs try Picamera2 first and fall back to OpenCV.
- A PCA9685 servo board on the Raspberry Pi's I²C bus: SDA to GPIO 2 (physical pin 3), SCL to GPIO 3 (physical pin 5), VCC (the board's logic supply, 3 to 5 V) to the Raspberry Pi's 3.3 V, GND to GND. The driver uses the board's default address, 0x40. The left arm's servo goes on channel 12, the right arm's servo on channel 15. (The other PCA9685 demo, [`demos/pca_servos.py`](../pca_servos.py), defaults to the opposite: left 15, right 12.) The two power notes in the docstring of `pca_servos.py` apply here too:
  > - Requires external 5V on PCA V+ for servos.
  > - Pi GND must be common with PCA GND.
- PRESSTO's printed parts, built as the [main README](../../README.md#assembly-instructions) describes: the base with the holders that clamp the phone, a camera arm, and two actuator arms over the phone, the left one over the left half of its screen, the right one over the right half. `cars_pca.py` drives one servo per arm, the one that presses (channels 12 and 15); nothing moves the arms' other servos. At the booth, the phone was touched by stylus tips grounded with Dupont wires.
- Optional: an LED on BCM17 (through a series resistor, its other leg to GND) and a push button on BCM27 (its other leg to GND; the program uses the internal pull-up). The bot runs without them.
- A phone running the game, in portrait orientation (at the booth it was not sideways): `calibrate.py` rectifies the screen to a portrait image of 360 × 640 pixels.

The booth's Raspberry Pi model, camera and phone, how its arms were mounted, and the package versions that ran there were not recorded.

## Install

1. Get this repository onto the Raspberry Pi, for example with `git clone https://github.com/crocs-muni/pressto.git`.
2. Enable I²C: run `sudo raspi-config`, open "Interface Options", select "I2C" and answer `Yes` (the current Raspberry Pi documentation gives the path `3 Interface Options > I5 I2C`). To check the wiring, install `i2c-tools` (`sudo apt install -y i2c-tools`): `i2cdetect -y 1` should list the PCA9685 at `40`.
3. Picamera2 (which brings the `libcamera` Python module) and GPIO Zero come with Raspberry Pi OS. If your image lacks them:
   ```
   sudo apt install -y python3-picamera2 python3-gpiozero
   ```
4. Since Raspberry Pi OS Bookworm, pip installs only into a virtual environment. Create one for this demo with `--system-site-packages`, so that it sees Picamera2 and GPIO Zero, and install the packages of [`requirements.txt`](requirements.txt): OpenCV, NumPy, the Adafruit PCA9685 driver and Adafruit Blinka (which provides `board` and `busio`). From the root of the repository:
   ```
   python3 -m venv --system-site-packages cars-env
   source cars-env/bin/activate
   python3 -m pip install -r demos/cars/requirements.txt
   ```
   Make a new environment even if you already have one for the other demos: an environment made without `--system-site-packages` does not see Picamera2 or GPIO Zero. `requirements.txt` names `opencv-python`, not a `-headless` OpenCV package, because `calibrate.py` and `cars_pca.py` open windows.

## Run

Run the programs in a terminal on the Raspberry Pi's desktop, from this folder: `calibrate.py` writes `calibration.json` into the current folder and `cars_pca.py` reads it from there. In every new terminal, first enter the environment, from the root of the repository:

```
source cars-env/bin/activate
cd demos/cars
```

OpenCV reads keys only while one of its windows has the focus. In `calibrate.py` a click inside the window also acts (it adds a corner or takes a sample), so give that window the focus by clicking its title bar.

### 1. Camera check: `test_camera.py`

```
python3 test_camera.py
```

It prints the Python and OpenCV versions, the `/dev/video*` devices and, if `v4l2-ctl` is installed, its device list (otherwise a line on how to install it, for information only), starts the camera, reads 30 frames and saves the last one as `cam_debug_frame.jpg`. The line `[cam] Picamera2 320x180 @…fps` or `[cam] OpenCV 320x180 @…fps` says how the camera was opened: through Picamera2 (a Raspberry Pi camera) or through OpenCV; the other `[cam]` lines report autofocus, OpenCV's settings, or why Picamera2 was not used. Open the picture to check that the camera sees the whole phone screen; with a Raspberry Pi camera its red and blue are swapped, which is expected (see step 2 of the calibration).

`calibrate.py` and `cars_pca.py` open a USB camera only as OpenCV device 0, through OpenCV's default backend (this check asks for V4L2), without the MJPG request and without this check's silent read retries: a camera that works here only with `--index`, `--mjpg` or `--force-opencv`, or only after failed reads, may not work in them (they always try Picamera2 first).

The options (`python3 test_camera.py --help` lists them too):

| Option | Default | What it does |
|---|---|---|
| `--width N` | `320` | frame width |
| `--height N` | `180` | frame height |
| `--index N` | `0` | OpenCV device index (only used for the OpenCV backend) |
| `--frames N` | `30` | how many frames to read |
| `--save FILE` | `cam_debug_frame.jpg` | where to save the last frame |
| `--probe` | off | only try the OpenCV device indices 0 to 9 and report each, then stop |
| `--mjpg` | off | ask an OpenCV camera for MJPG (USB webcams often like this) |
| `--force-opencv` | off | use OpenCV, skip Picamera2 |
| `--force-picam2` | off | use Picamera2 only (see [Known issues](#known-issues)) |

### 2. Calibration: `calibrate.py`

```
python3 calibrate.py
```

The calibration is part of the initial setup, done by hand: it tells the bot where the phone's screen lies in the camera image and what the game's colours look like to your camera under your lighting. The window shows the live camera image on the left. Once the game area is marked, the right panel shows it rectified, squeezed to the size of the camera image, with the four lanes and the decision line: the bot acts on objects that come close to that line.

1. On the phone, open the game's calibration screen: hold a finger on its start screen ("tap to start") for 5 seconds. It shows one object to collect (a green circle) and one to avoid (a red square) on the blue background.
2. Keep the default resolution, 320 × 180: `cars_pca.py` always captures at 320 × 180, and `calibration.json` does not record the resolution. The game must appear upright in the left panel, as a player sees it (its text readable). If the image is mirrored or turned, or its red and blue are swapped (with a Raspberry Pi camera they always are), fix it now with `H`, `V`, `T` or `X`, before step 3: these settings are saved with the calibration and shape the still copy that `Space` takes. Do not change them after `Space`: if you do, press `Space` and mark the corners again, and after `X` also take the three colour samples again.
3. Press `Space`: the program keeps a still copy of the image (the left panel stays live). Click the four corners of the phone's screen in the left panel, in any order, and press `Enter` (the window asks for top-left, top-right, bottom-right, bottom-left, but the program sorts the corners by their position, so the orientation comes only from step 2). The game fills the whole screen, draws its four lanes over the full width and its cars at 88 % of the height, which is where `cars_pca.py` expects them. The right panel now shows the rectified still copy: the circle should sit in the middle of the second lane, the square in the middle of the third. If not, correct the orientation (step 2), then press `Space` and mark the corners again.
4. Press `G` and click the green circle, `B` and click the red square, `E` and click the background, all in the right panel.
5. Press `Y` and click where the decision line should be, or move it with `[` and `]`; it starts at 80 % of the height.
6. Press `S`: the terminal shows `[save] Wrote …/calibration.json`. `S` saves the corners accepted with the last `Enter` together with the three colours; until both exist, it does nothing and prints nothing.
7. Quit with `Q` before you start `cars_pca.py`: a Raspberry Pi camera can be used by only one program at a time. Calibrate again whenever the camera, the phone or the holders move, or the lighting changes.

#### Keys of `calibrate.py`

Letters work in either case.

| Key | Action |
|-----|---|
| `Q`, `Esc` | quit |
| `Space` | keep a still copy of the camera image to mark the corners on (the left panel stays live; starts the marking over) |
| click (left mouse button) | while marking: add a corner, up to four, wherever you click; in the right panel after `G`, `B`, `E` or `Y`: take that colour sample or set the decision line — the mode stays, so every further click there replaces it |
| `U` | remove the last corner (while marking) |
| `Enter` | accept the four corners and show the rectified still copy |
| `G`, `B`, `E` | sample mode: the colour to collect, to avoid, or of the empty background (clicks in the right panel) |
| `Y` | decision-line mode (clicks in the right panel) |
| `[`, `]` | move the decision line up, down by 1 % of the height (between 50 % and 95 %) |
| `R` | clear the colour samples and leave the sample mode (keeps the corners) |
| `S` | save `calibration.json`: the corners accepted with the last `Enter` and the three colours (until both exist, nothing happens) |
| `H`, `V` | flip the image horizontally, vertically (the on-screen hint calls H, V and T "rotate") |
| `T` | rotate the image by 90 degrees |
| `X` | swap red and blue |
| `1`, `2`, `3` | camera resolution 320 × 180, 480 × 270, 640 × 360; calibrate at 320 × 180 (step 2, and see [Known issues](#known-issues)) |
| `F` | refocus a USB camera with autofocus (no effect with Picamera2, which keeps autofocusing on its own) |

### 3. Play: `cars_pca.py`

```
python3 cars_pca.py
```

The window shows the rectified game: the lane numbers, the decision line, a thin line where the scanned area ends and the car line (where the cars are expected; with the default settings the two nearly coincide), with, above them, the edge of the band that detection ignores; the nearest object per lane (`G` to collect, `R` to avoid), green or red ticks where an object crosses the decision line, where the bot believes the cars are (`L@n`, `R@n`), its plan for each side and a status line (most of which is cut off, see [Known issues](#known-issues)).

The bot starts in HUMAN mode: it does not tap on its own. Check the arms first, the first time with the styluses clear of the phone:

- The first tap, whether from a test key or from the bot, also sends the other servo to its rest angle; the tapping one goes straight to its press angle. The angles: rest 70° and press 160° for the left servo (channel 12), rest 150° and press 90° for the right one (channel 15), each tap held for 0.10 s. These are the booth's values; set yours in `LEFT_REST_DEG`, `LEFT_PRESS_DEG`, `RIGHT_REST_DEG` and `RIGHT_PRESS_DEG` near the top of `cars_pca.py`.
- `1` and `2` tap the left and the right side. If the wrong arm moves, swap the two servo plugs on the PCA9685: each channel keeps its own angles, and `S` only exchanges the sides.

Then leave the game's calibration screen (double-tap it) and let the bot play:

- With the game's start screen ("tap to start") or game-over screen ("tap to play again") showing, press `B` (or the button): after 5 seconds the bot taps the right side once, which starts a game, assumes both cars are in the middle lanes (1 and 2), waits 1.5 s and plays (BOT mode). In BOT mode, `B` returns to HUMAN mode; during the countdown it only restarts the countdown (to stop the arming, quit with `Q`). Do not start the game by hand: the bot's tap is what starts it, and on a running game that tap would move the right car while the bot assumes it is still in a middle lane.
- While it plays, it taps when an object to avoid comes close to the decision line in a car's lane, or an object to collect comes close in that car's other lane, unless that other lane is blocked by an object to avoid; each side waits at least 0.22 s between taps.
- If nothing crosses the decision line for 7 seconds, it takes the game as over: it taps the right side once more ("tap to play again") and starts again from the middle lanes.
- The LED is off in HUMAN mode, blinks while arming and is on in BOT mode.

#### Keys of `cars_pca.py`

Letters work in either case, except `r`.

| Key | Action |
|-----|---|
| `Q`, `Esc` | quit (if a tap has opened the PCA9685, both servos return to rest) |
| `B` | arm the bot (HUMAN → 5 s → BOT), or back to HUMAN; pressed while arming, it restarts the 5 s |
| `1`, `2` | test tap: left side, right side (in every mode; in BOT mode the bot does not notice that the car moved, so test in HUMAN mode) |
| `S` | swap the sides (left ↔ right); each channel keeps its angles |
| `r` | lower case only: reset where the bot believes the cars are (both in the middle lanes) |
| `L` | reload `calibration.json` (this also resets the decision line to its saved value) |
| `[`, `]` | move the decision line up, down by 1 % of the height |
| `-`, `=` | scan less, more of the image below the decision line (0 % to 30 %) |
| `,`, `.` | make the ignored band above the cars smaller, larger (1 % to 12 % of the height; it never reaches higher than 2 % below the decision line) |
| `I` | ignore the band above the cars in detection: on / off |
| `O` | shade the ignored band in the picture: on / off |
| `D` | overlay (lanes, markers, plan): on / off |
| `C` | show only the detected colours: on / off |
| `F` | refocus a USB camera with autofocus (no effect with Picamera2) |

At start the ignored band is on, its shading off, the overlay on, the colours-only view off and the sides not swapped. Nothing changed with these keys is saved.

## Files the programs write

| File | Written by | Read by |
|---|---|---|
| `calibration.json` | `calibrate.py` (`S`), in the current folder | `cars_pca.py`, from the current folder, at start and on `L` |
| `cam_debug_frame.jpg` | `test_camera.py` (the default of `--save`), in the current folder | you |

`cars_pca.py` writes no file; it prints what it does in the terminal.

## Good to know

- `Q`, `Esc`, Ctrl+C in the terminal, `kill` (SIGTERM) and closing the terminal (SIGHUP, also under `nohup`) all end `cars_pca.py` through its clean-up, which first returns both servos to rest (once a tap has opened the PCA9685). A tap interrupted during its 0.10 s hold releases its servo at once.
- A servo can still stay pressed if one of these happens during a tap: `kill -9` (SIGKILL), Ctrl+\ (SIGQUIT), a crash of the Python process (also inside OpenCV or the camera library), or the Raspberry Pi losing power while the servo board keeps its own supply. No clean-up runs then, and the PCA9685 keeps sending the last pulse until the next tap of a later run or until the board loses power. The same can happen if the servo board stops answering on I²C during a release (a loose wire, a supply dip: the release fails and the program ends with that error), or if a second interrupt arrives before the clean-up has finished. Ctrl+Z pauses the program without any clean-up, with a servo caught mid-tap still pressed.
- In BOT mode the right arm taps every 7 seconds for as long as nothing crosses the decision line, whether a game is on the screen or not: press `B` to stop it.
- Taps need the PCA9685 driver and the board: without them `cars_pca.py` starts, but its first tap ends it with an error. The message "PCA9685 library not available. Install with: pip3 install adafruit-circuitpython-pca9685" appears when `adafruit_pca9685`, `board` or `busio` cannot be imported; install `requirements.txt` into the environment you run the program in (step 4 of Install) instead of running that line.
- With GPIO Zero installed (as on Raspberry Pi OS), `cars_pca.py` uses BCM17 as an output and BCM27 as an input whether or not an LED and a button are wired.
- "calibration.json not found. Run the setup tool first." means: run `calibrate.py` first, in this folder.

## Known issues

- In `calibrate.py` and `cars_pca.py`, arrow and page keys can act as letters: OpenCV keeps only the low 8 bits of a key code, and the Left arrow's code 0xFF51 then reads as `Q`. So Left quits, Right acts as `S` (swaps the sides in `cars_pca.py`, saves in `calibrate.py`), Up as `R` (clears the samples in `calibrate.py`), Down as `T` (rotates the image in `calibrate.py`), Page Up as `U` (removes a corner) and Page Down as `V` (flips the image). Avoid them.
- On-screen text is wider than the image and is cut off at its right edge. `cars_pca.py`'s status line shows little more than the resolution, the frame rate and the mode; the side mapping, the scan limit and the arming countdown are drawn past the edge, and the plan lines lose their ends. At 320 × 180, `calibrate.py`'s help lines are cut after about 30 characters. (Where it does show, `≤`, `≥` or `°` appears as `???` or `??`: the font the programs use draws only ASCII characters.)
- `calibrate.py` with Picamera2: the resolution keys `1`, `2` and `3` end the program with an error, because the camera is opened again while it is still held.
- `test_camera.py --force-picam2`: when Picamera2 cannot start, the program prints `[cam] OpenCV 320x180 @unknownfps` and then stops with an `AttributeError` instead of its message "Forced Picamera2 but it failed to start."

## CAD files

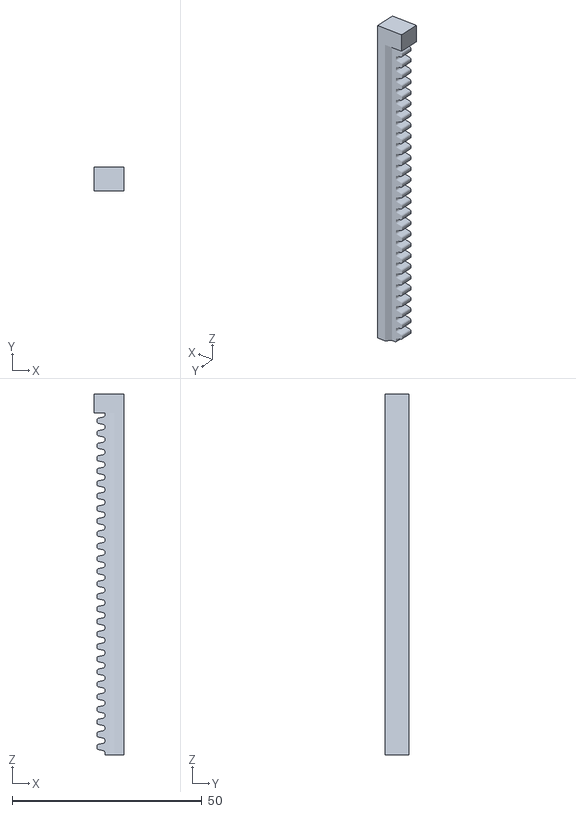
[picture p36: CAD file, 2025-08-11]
stl/actuator_arm/actuator_arm_rack.stl
8.00 x 6.35 x 95.0

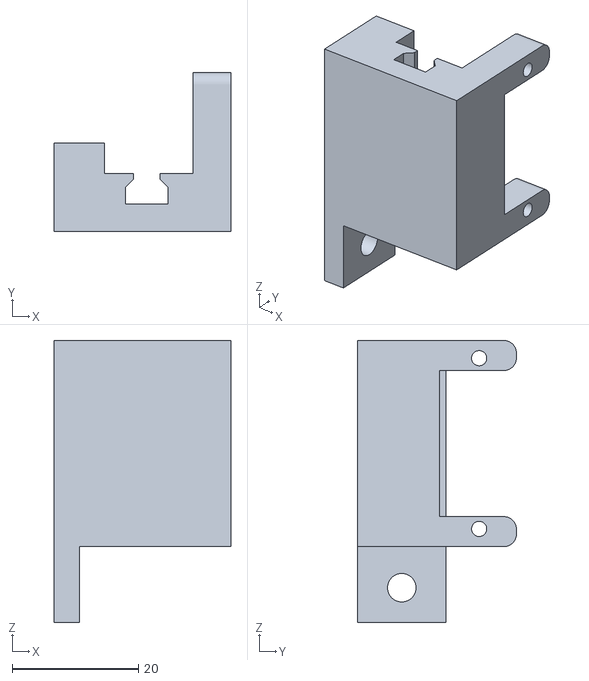
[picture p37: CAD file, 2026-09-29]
stl/actuator_arm_base/actuator_arm_base_motor_holder_single_hole.stl
28.0 x 25.1 x 44.6

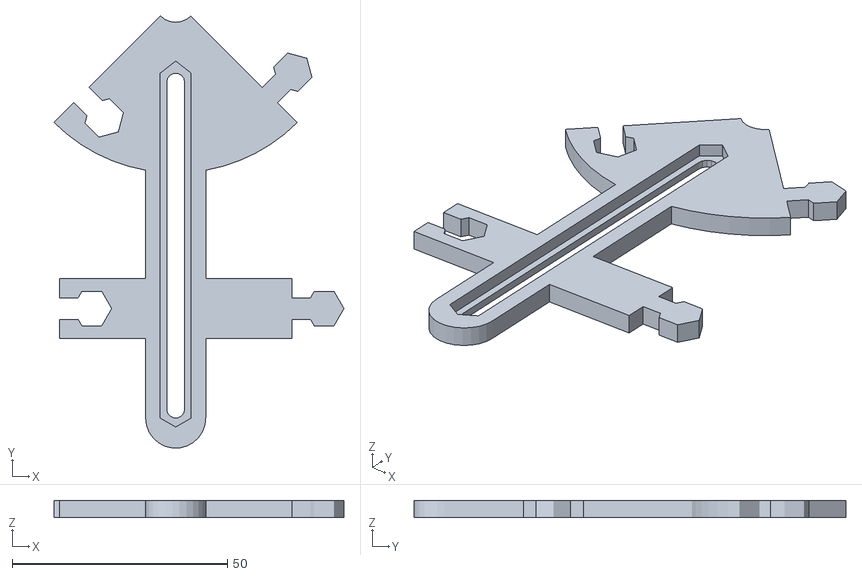
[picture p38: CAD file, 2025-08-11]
stl/base/base_inner.stl
67.4 x 100.4 x 4.00

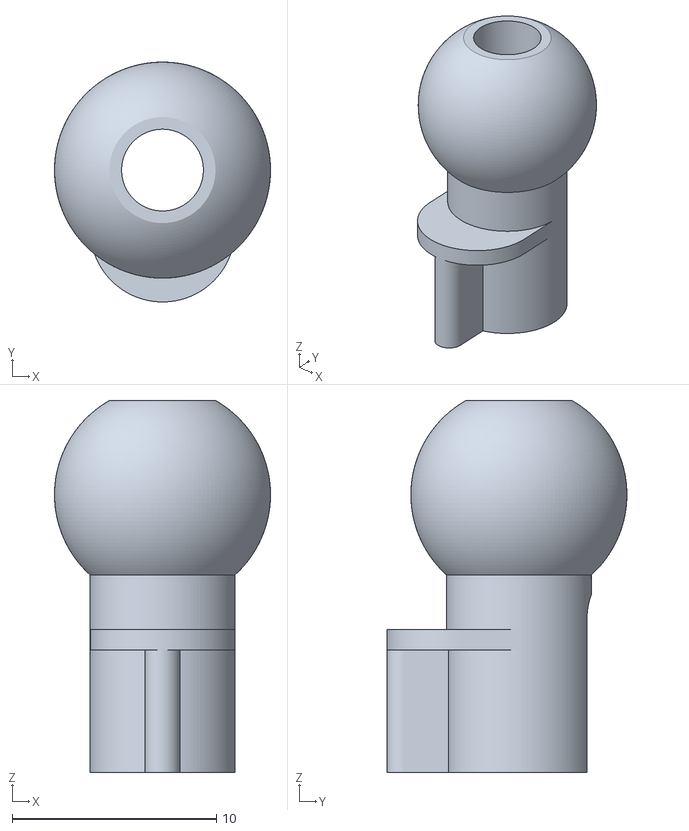
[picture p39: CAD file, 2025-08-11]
stl/camera_arm/arm_base.stl
10.6 x 11.7 x 18.2

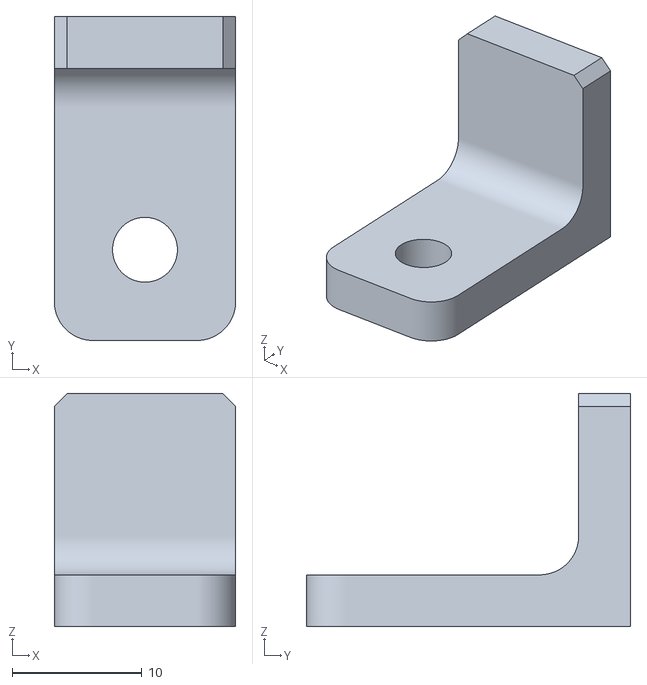
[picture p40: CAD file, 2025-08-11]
stl/holder/holder.stl
14.0 x 25.0 x 18.0

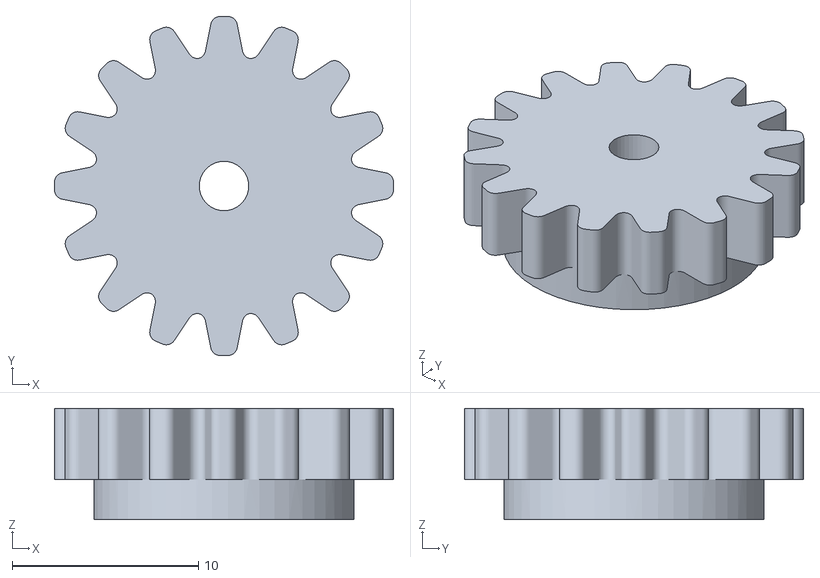
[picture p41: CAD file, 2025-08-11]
stl/pinion_gear/pinion_gear.stl
18.2 x 18.2 x 5.97

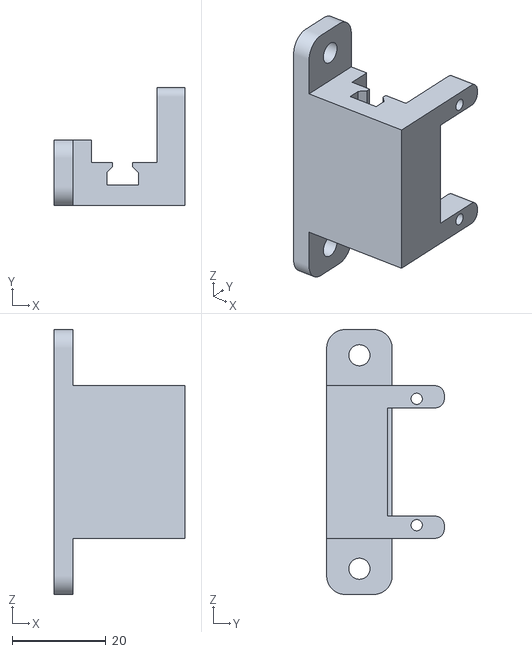
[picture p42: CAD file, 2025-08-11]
stl/actuator_arm/actuator_arm_motor_holder.stl
28.0 x 25.1 x 56.6

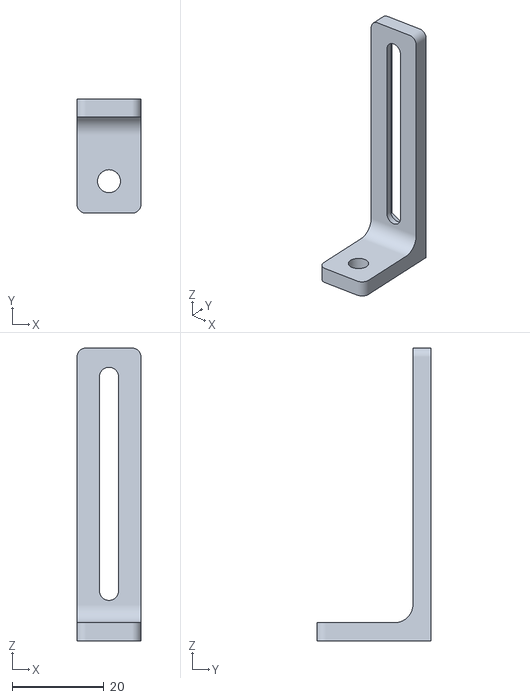
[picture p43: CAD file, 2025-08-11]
stl/actuator_arm_base/actuator_arm_base_stand.stl
14.0 x 25.0 x 64.0

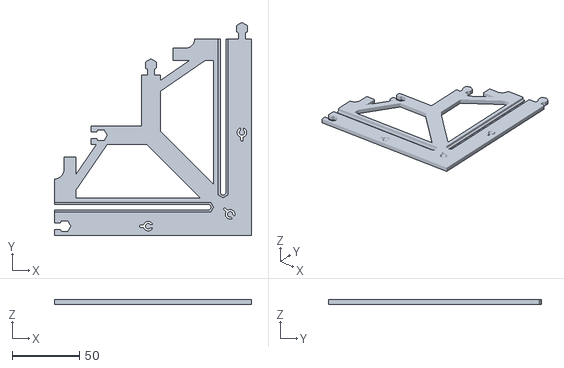
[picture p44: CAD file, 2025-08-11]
stl/base/base_outer.stl
146.1 x 158.1 x 4.00

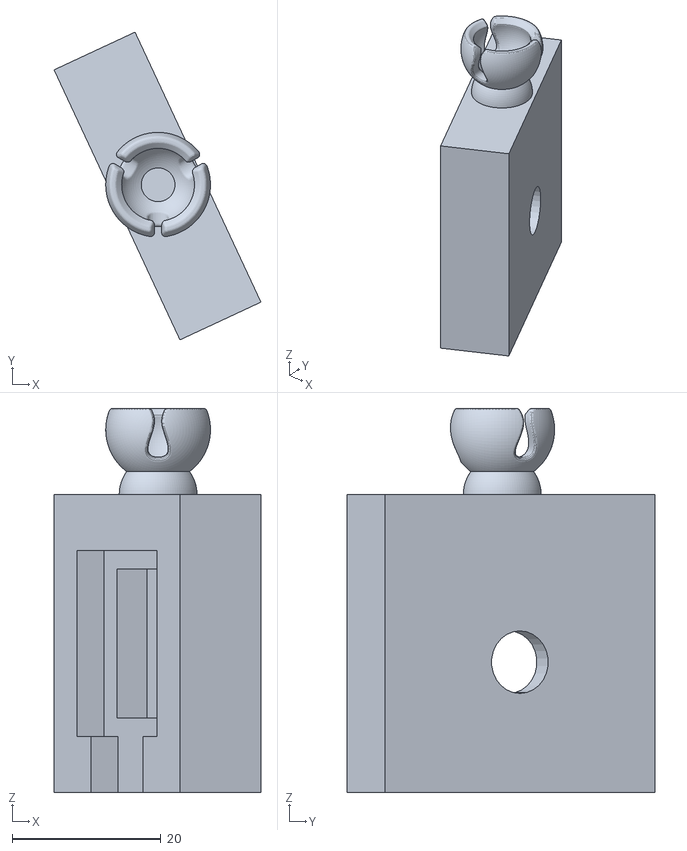
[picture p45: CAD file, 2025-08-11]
stl/camera_arm/camera_holder.stl
27.8 x 41.3 x 51.6

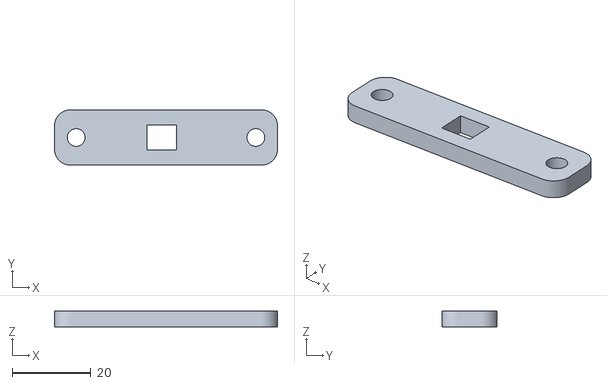
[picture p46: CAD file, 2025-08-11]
stl/actuator_arm/actuator_arm_motor_holder_mount.stl
56.6 x 14.0 x 4.00

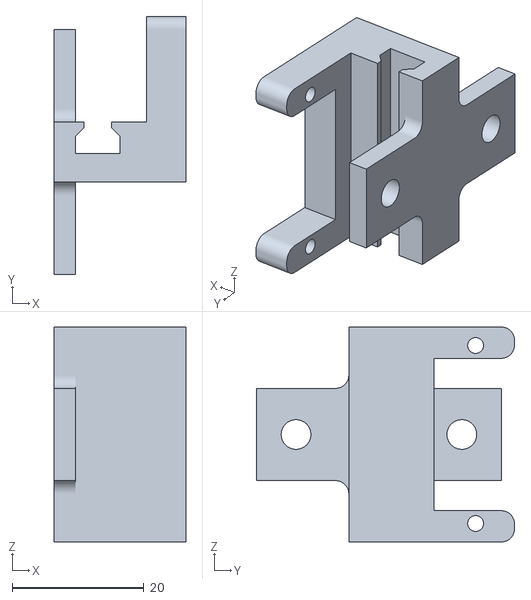
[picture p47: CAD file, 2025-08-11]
stl/actuator_arm_base/actuator_arm_base_motor_holder.stl
20.0 x 39.1 x 32.6

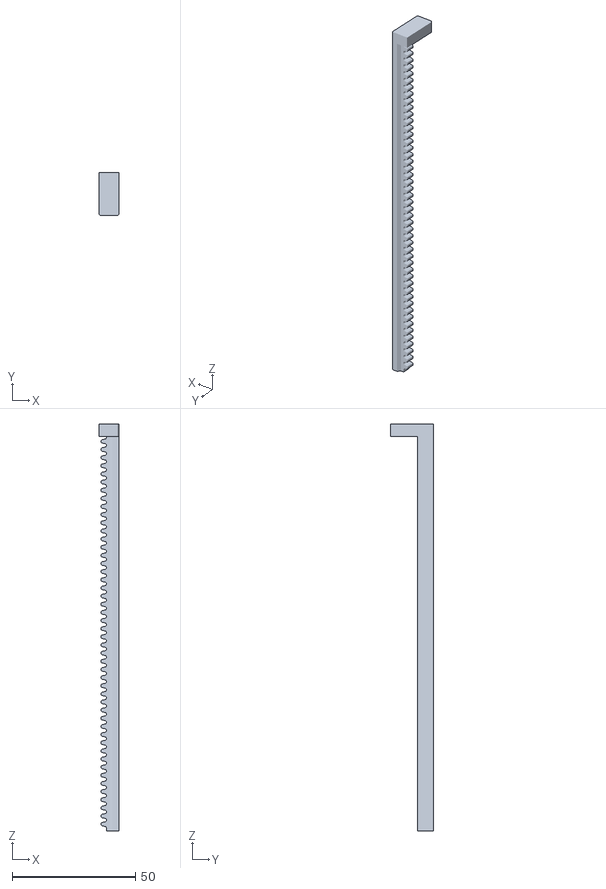
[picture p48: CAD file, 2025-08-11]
stl/actuator_arm/actuator_arm_rack_wide.stl
8.00 x 17.4 x 165.0

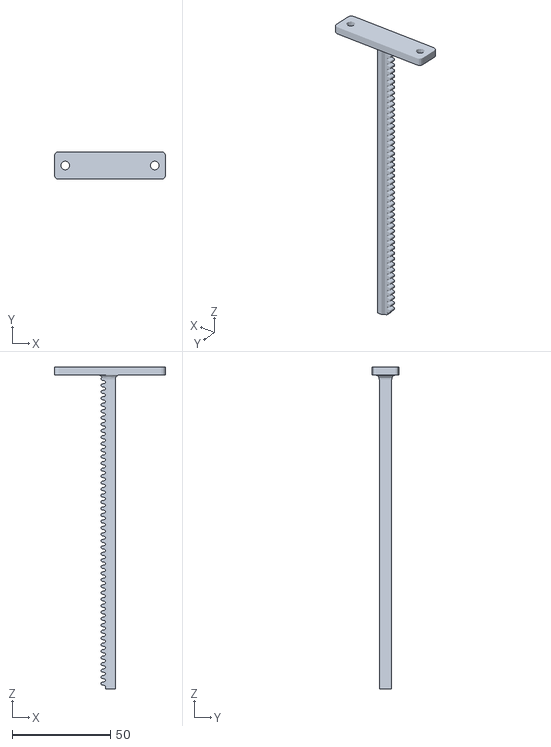
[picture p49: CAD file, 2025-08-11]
stl/actuator_arm_base/actuator_arm_base_rack_with_mount.stl
56.6 x 14.0 x 164.0

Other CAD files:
ipt/actuator_arm/actuator_arm_motor_holder.ipt
ipt/actuator_arm/actuator_arm_motor_holder_mount.ipt
ipt/actuator_arm/actuator_arm_rack.ipt
ipt/actuator_arm/actuator_arm_rack_wide.ipt
ipt/actuator_arm_base/actuator_arm_base_motor_holder.ipt
ipt/actuator_arm_base/actuator_arm_base_motor_holder_single_hole.ipt
ipt/actuator_arm_base/actuator_arm_base_rack.ipt
ipt/actuator_arm_base/actuator_arm_base_rack_with_mount.ipt
ipt/actuator_arm_base/actuator_arm_base_stand.ipt
ipt/base/base_inner.ipt
ipt/base/base_outer.ipt
ipt/camera_arm/arm_base.ipt
ipt/camera_arm/ball_joint.ipt
ipt/camera_arm/camera_holder.ipt
ipt/holder/holder.ipt
ipt/pinion_gear/pinion_gear.ipt

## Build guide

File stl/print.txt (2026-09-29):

- Recommended print settings:
  - Material: PLA or PETG
  - Layer Height: 0.15 mm
  - Infill: 15–30% for strength
  - Supports: As needed per part

4 x base_inner
4 x base_outer
4 x holder
2 x arm_base
2 x camera_holder
20 x ball_joint
10 x pinion_gear
10 x actuator_arm_motor_holder
10 x actuator_arm_base_rack
10 x actuator_arm_base_stand
10 x actuator_arm_motor_holder_mount
10 x actuator_arm_base_motor_holder
10 x actuator_arm_base_motor_holder_single_hole
6 x actuator_arm_rack
6 x actuator_arm_rack_wide

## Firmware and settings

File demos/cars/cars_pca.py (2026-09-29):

#!/usr/bin/env python3
# Two-Cars bot with:
# - HUMAN/BOT modes (+ ARMING delay), auto-restart
# - LED (BCM17) status: OFF/HUMAN, BLINK/ARMING, ON/BOT
# - Button (BCM27): same as 'B' key toggle
# - Servo mapping swap + test taps
# - Sanity view, decision inspector, tripwire, visible bottom (optional shading)
# - Ignore-bottom band (removes cars from detection)
# - Decision line fully adjustable (0.0–1.0)
# - ROI scan: only detect above decision line (+ adjustable margin)
"""The cars demo's bot: PRESSTO plays a two-cars phone game.

A camera watches the phone's screen (Picamera2, or OpenCV camera 0 when
Picamera2 cannot be started). Each frame is rectified with calibration.json,
objects are found by their calibrated colours in four lanes, and two servo
arms on a PCA9685 (I2C, channel 12 = left, channel 15 = right) tap the phone
so that each car switches lanes: towards a good (green) object, away from a
bad (red) one.

Usage, on the Raspberry Pi, in the folder that holds calibration.json
(written by calibrate.py):

    python3 cars_pca.py

Needs a display: the program shows an OpenCV window and reads its keys from
that window. It starts in HUMAN mode, in which the bot does not tap on its
own; B (or the optional button on BCM27) arms it, and 5 s later it taps once
and plays (BOT mode). Q or Esc quits. README.md next to this file lists
every key.
"""

import json, signal, time
from pathlib import Path
import cv2
import numpy as np

# --- Servo control (PCA9685 on I2C; channels 15 and 12) ---
try:
    import board
    import busio
    from adafruit_pca9685 import PCA9685
    _PCA_AVAILABLE = True
except Exception:
    PCA9685 = None
    _PCA_AVAILABLE = False

# Tune these if your button press needs different travel.
SERVO_FREQ_HZ = 50
SERVO_MIN_US  = 500
SERVO_MAX_US  = 2500

# Physical channels on the PCA9685 (as wired):
LEFT_CH  = 12
RIGHT_CH = 15

# Default angles (degrees) for each servo.
# REST = not pressing; PRESS = pressing the button.
LEFT_REST_DEG  = 70
LEFT_PRESS_DEG = 160
RIGHT_REST_DEG  = 150
RIGHT_PRESS_DEG = 90

PRESS_HOLD_S = 0.10

_pca = None
_i2c = None

def _clamp(x, lo, hi):
    return lo if x < lo else hi if x > hi else x

def _angle_to_pulse_us(angle_deg: float) -> int:
    a = _clamp(float(angle_deg), 0.0, 180.0)
    return int(SERVO_MIN_US + (a / 180.0) * (SERVO_MAX_US - SERVO_MIN_US))

def _pulse_us_to_duty(pulse_us: int, freq_hz: int) -> int:
    period_us = 1_000_000 / float(freq_hz)
    duty = int((pulse_us / period_us) * 0xFFFF)
    return int(_clamp(duty, 0, 0xFFFF))

def _get_pca():
    global _pca, _i2c
    if _pca is not None:
        return _pca
    if not _PCA_AVAILABLE:
        raise RuntimeError(
            "PCA9685 library not available. Install with: pip3 install adafruit-circuitpython-pca9685"
        )
    _i2c = busio.I2C(board.SCL, board.SDA)
    _pca = PCA9685(_i2c)
    _pca.frequency = SERVO_FREQ_HZ
    # Initialize to REST so we don't slam on first press.
    _set_angle(LEFT_CH, LEFT_REST_DEG)
    _set_angle(RIGHT_CH, RIGHT_REST_DEG)
    return _pca

def _set_angle(channel: int, angle_deg: float):
    pca = _get_pca()
    pulse = _angle_to_pulse_us(angle_deg)
    pca.channels[int(channel)].duty_cycle = _pulse_us_to_duty(pulse, SERVO_FREQ_HZ)

def press_left():
    _set_angle(LEFT_CH, LEFT_PRESS_DEG)
    try:
        time.sleep(PRESS_HOLD_S)
    finally:
        _set_angle(LEFT_CH, LEFT_REST_DEG)   # released even when the hold is interrupted

def press_right():
    _set_angle(RIGHT_CH, RIGHT_PRESS_DEG)
    try:
        time.sleep(PRESS_HOLD_S)
    finally:
        _set_angle(RIGHT_CH, RIGHT_REST_DEG)   # released even when the hold is interrupted

def press_both():
    # Near-simultaneous: set both, hold, then release both.
    try:
        _set_angle(LEFT_CH, LEFT_PRESS_DEG)
        _set_angle(RIGHT_CH, RIGHT_PRESS_DEG)
        time.sleep(PRESS_HOLD_S)
    finally:
        try:
            _set_angle(LEFT_CH, LEFT_REST_DEG)
        finally:
            _set_angle(RIGHT_CH, RIGHT_REST_DEG)

def close():
    global _pca
    if _pca is not None:
        try:
            # Return to REST on exit
            _set_angle(LEFT_CH, LEFT_REST_DEG)
            _set_angle(RIGHT_CH, RIGHT_REST_DEG)
        except Exception:
            pass
        try:
            _pca.deinit()
        except Exception:
            pass
        _pca = None


CALIB_PATH = Path("calibration.json")

# --- GPIO: LED + Button (optional; app runs without them) ---
LED_PIN = 17       # BCM17 for LED (series resistor required)
BUTTON_PIN = 27    # BCM27 for button (other leg to GND; internal pull-up)

try:
    from gpiozero import LED, Button
    _GPIO_AVAILABLE = True
except Exception:
    LED = Button = None
    _GPIO_AVAILABLE = False

# ---------- Camera ----------
class Camera:
    def __init__(self, width=320, height=180):
        self.picam2 = None
        self.cap = None
        self.w, self.h = width, height
        self.fps, self.has_autofocus = None, False
        self.libcamera = None
        self._start_picam2() or self._start_opencv()

    def _start_picam2(self):
        try:
            from picamera2 import Picamera2
            import libcamera
            self.libcamera = libcamera
            self.picam2 = Picamera2()
            for f in (120, 90, 60, 30):
                try:
                    cfg = self.picam2.create_video_configuration(
                        main={"size": (self.w, self.h), "format": "RGB888"},
                        controls={"FrameDurationLimits": (int(1e6/f), int(1e6/f))}
                    )
                    self.picam2.configure(cfg); self.picam2.start(); time.sleep(0.15); self.fps = f; break
                except Exception:
                    try: self.picam2.stop()
                    except Exception: pass
                    self.picam2 = Picamera2()
            try:
                self.picam2.set_controls({"AfMode": self.libcamera.controls.AfModeEnum.Continuous})
                self.has_autofocus = True
            except Exception:
                pass
            return True
        except Exception:
            self.picam2 = None
            return False

    def _start_opencv(self):
        self.cap = cv2.VideoCapture(0)
        if not self.cap.isOpened(): raise RuntimeError("No camera")
        self.cap.set(cv2.CAP_PROP_FRAME_WIDTH, self.w)
        self.cap.set(cv2.CAP_PROP_FRAME_HEIGHT, self.h)
        for f in (120, 90, 60, 30):
            if self.cap.set(cv2.CAP_PROP_FPS, f): self.fps = f; break
        try:
            if hasattr(cv2, "CAP_PROP_AUTOFOCUS"):
                self.cap.set(cv2.CAP_PROP_AUTOFOCUS, 1); self.has_autofocus = True
        except Exception:
            pass

    def refocus(self):
        if self.picam2 is not None and self.has_autofocus:
            try: self.picam2.set_controls({"AfTrigger": self.libcamera.controls.AfTrigger.Start})
            except Exception: pass
        elif self.cap is not None and self.has_autofocus:
            try: self.cap.set(cv2.CAP_PROP_AUTOFOCUS, 0); time.sleep(0.05); self.cap.set(cv2.CAP_PROP_AUTOFOCUS, 1)
            except Exception: pass

    def read(self):
        if self.picam2 is not None:
            rgb = self.picam2.capture_array()
            return cv2.cvtColor(rgb, cv2.COLOR_RGB2BGR)
        ok, frame = self.cap.read()
        if not ok: raise RuntimeError("Capture failed")
        return frame

    def release(self):
        if self.picam2 is not None:
            try: self.picam2.stop()
            except Exception: pass
        if self.cap is not None:
            self.cap.release()

# ---------- Utils ----------
def apply_preproc(img, pp):
    out = img
    if pp.get("swap_rb"): out = out[..., ::-1]
    rk = int(pp.get("rotate_k", 0))
    if rk: out = np.ascontiguousarray(np.rot90(out, k=rk))
    if pp.get("flip_h"): out = cv2.flip(out, 1)
    if pp.get("flip_v"): out = cv2.flip(out, 0)
    return out

def hsv_mask(img_bgr, ranges):
    hsv = cv2.cvtColor(img_bgr, cv2.COLOR_BGR2HSV)
    out = np.zeros(hsv.shape[:2], dtype=np.uint8)
    for lo, hi in ranges:
        out |= cv2.inRange(hsv, np.array(lo, np.uint8), np.array(hi, np.uint8))
    return out

def find_objects(mask, min_area=40):
    contours, _ = cv2.findContours(mask, cv2.RETR_EXTERNAL, cv2.CHAIN_APPROX_SIMPLE)
    objs = []
    for c in contours:
        a = cv2.contourArea(c)
        if a < min_area: continue
        m = cv2.moments(c)
        if m["m00"] == 0: continue
        cx = int(m["m10"] / m["m00"]); cy = int(m["m01"] / m["m00"])
        objs.append((cx, cy, a))
    return objs

# ---------- Bot ----------
class TwoCarsBot:
    def __init__(self, calib):
        self.load_from_calib(calib)
        # Cars spawn in inner lanes
        self.left_lane  = 1
        self.right_lane = 2
        # Timing & margins
        self.last_press_L = 0.0
        self.last_press_R = 0.0
        self.cooldown_s = 0.22
        self.trigger_margin = int(self.H * 0.12)
        self.collect_margin = int(self.H * 0.16)
        self.safety_gap     = int(self.H * 0.14)
        # Servo mapping (False = L->left, R->right; True = swapped)
        self.servo_swap = False

    def load_from_calib(self, calib):
        self.W = int(calib["rectified_size"]["w"])
        self.H = int(calib["rectified_size"]["h"])
        self.warpM = np.array(calib["warp_matrix"], dtype=np.float32)
        self.pp = calib.get("preprocess", {})
        self.lanes = int(calib.get("lanes", 4))
        self.decision_y_frac = float(calib.get("decision_y_frac", 0.80))
        self.car_y_frac = float(calib.get("car_y_frac", 0.88))
        self.good_ranges = calib["good_hsv_ranges"]
        self.bad_ranges  = calib["bad_hsv_ranges"]

    def lane_of_x(self, x):
        return int(np.clip(x * self.lanes // self.W, 0, self.lanes - 1))

    def rect_frame(self, frame):
        frame = apply_preproc(frame, self.pp)
        return cv2.warpPerspective(frame, self.warpM, (self.W, self.H))

    # ---------- Servo helpers ----------
    def tap_side(self, side):
        """Tap the correct physical servo for a logical side ('L' or 'R')."""
        if not self.servo_swap:
            press_left()  if side == "L" else press_right()
        else:
            press_right() if side == "L" else press_left()

    # ---- Decision planning (no side effects) ----
    def plan(self, objs_good, objs_bad, now_s):
        y_dec = int(self.H * self.decision_y_frac)
        nearest_good = [None]*self.lanes
        nearest_bad  = [None]*self.lanes

        def upd(bucket, lane, obj):
            if obj[1] >= y_dec:  # ignore below decision line
                return
            if bucket[lane] is None or obj[1] > bucket[lane][1]:
                bucket[lane] = obj

        for (cx, cy, a) in objs_good:
            upd(nearest_good, self.lane_of_x(cx), (cx, cy, a))
        for (cx, cy, a) in objs_bad:
            upd(nearest_bad,  self.lane_of_x(cx), (cx, cy, a))

        def side_plan(cur_lane, lanes, last_press_time):
            other = lanes[1] if cur_lane == lanes[0] else lanes[0]
            bad_cur   = nearest_bad[cur_lane]
            bad_other = nearest_bad[other]
            good_other= nearest_good[other]
            cd = max(0.0, self.cooldown_s - (now_s - last_press_time))
            will = False; reason = "NONE"
            if cd > 0:
                reason = "COOLDOWN"
            else:
                if bad_cur is not None and bad_cur[1] >= y_dec - self.trigger_margin:
                    if bad_other is not None and bad_other[1] >= y_dec - self.safety_gap:
                        reason = "BLOCKED"
                    else:
                        will = True; reason = "DODGE"
                elif good_other is not None and good_other[1] >= y_dec - self.collect_margin:
                    if bad_other is not None and bad_other[1] >= y_dec - self.safety_gap:
                        reason = "BLOCKED"
                    else:
                        will = True; reason = "COLLECT"
            return {
                "cur": cur_lane, "other": other, "y_dec": y_dec,
                "will_press": will, "reason": reason, "cd_remain": cd,
                "bad_cur": bad_cur, "bad_other": bad_other, "good_other": good_other,
            }

        planL = side_plan(self.left_lane,  (0,1), self.last_press_L)
        planR = side_plan(self.right_lane, (2,3), self.last_press_R)
        return {"L": planL, "R": planR}

    def execute_plan(self, plan, now_s):
        if plan["L"]["will_press"] and plan["L"]["cd_remain"] <= 0:
            self.tap_side("L")
            self.left_lane = 1 if self.left_lane == 0 else 0
            self.last_press_L = now_s
            print(f"[act] LEFT  -> toggle ({plan['L']['reason']})")
        if plan["R"]["will_press"] and plan["R"]["cd_remain"] <= 0:
            self.tap_side("R")
            self.right_lane = 3 if self.right_lane == 2 else 2
            self.last_press_R = now_s
            print(f"[act] RIGHT -> toggle ({plan['R']['reason']})")

    def sync_to_game_start(self):
        """Align our internal lane memory with the game's spawn state (both cars center)."""
        self.left_lane, self.right_lane = 1, 2
        self.last_press_L = self.last_press_R = 0.0

# ---------- Helpers for overlay/debug ----------
def lane_center_x(lane, W, lanes):
    x0 = int(lane * W / lanes)
    x1 = int((lane+1) * W / lanes)
    return (x0 + x1)//2

def nearest_per_lane(objs, W, lanes):
    buckets = [None]*lanes
    for (cx, cy, a) in objs:
        lane = int(np.clip(cx * lanes // W, 0, lanes-1))
        if buckets[lane] is None or cy > buckets[lane][1]:
            buckets[lane] = (cx, cy, a)
    return buckets

def lane_hits(band_hits_boolvec, W, lanes):
    xs = np.where(band_hits_boolvec)[0]
    if xs.size == 0: return []
    hit_lanes = set()
    for x in xs:
        lane = int(np.clip(x * lanes // W, 0, lanes-1))
        hit_lanes.add(lane)
    return sorted(list(hit_lanes))

# ---------- Main loop with modes ----------
def main():
    if not CALIB_PATH.exists():
        print("calibration.json not found. Run the setup tool first.")
        return

    calib = json.loads(CALIB_PATH.read_text())
    bot = TwoCarsBot(calib)
    cam = Camera(width=320, height=180)

    win = "TwoCarsBot - Runtime"
    cv2.namedWindow(win, cv2.WINDOW_NORMAL)

    # GPIO hardware (graceful if not available)
    led = LED(LED_PIN) if _GPIO_AVAILABLE else None
    if led is not None: led.off()
    button = Button(BUTTON_PIN, pull_up=True, bounce_time=0.05) if _GPIO_AVAILABLE else None
    prev_button = False  # edge detect

    def update_led(now):
        if led is None: return
        if mode == MODE_HUMAN:
            led.off()
        elif mode == MODE_ARMING:
            # blink ~4 Hz
            led.on() if int(now * 4) % 2 == 0 else led.off()
        else:  # MODE_BOT
            led.on()

    # Modes
    MODE_HUMAN, MODE_ARMING, MODE_BOT = 0, 1, 2
    mode = MODE_HUMAN
    arming_until = 0.0
    grace_until  = 0.0

    # Game-over detection
    last_pass_time = time.time()
    pass_timeout_s = 7.0
    arming_delay_s = 5.0

    # Ignore-bottom band (to remove cars from detection)
    ignore_enabled = True
    ignore_band_above_car = 0.05   # fraction of height above car line to ignore

    # Scan ROI margin below decision line (fraction of H)
    scan_margin_frac = 0.08        # tune with '-' and '='

    kernel = np.ones((3,3), np.uint8)
    t_last = time.time()

    debug_overlay = True
    sanity_view = False
    last_trip_g = last_trip_r = 0.0
    show_ignore_shading = False   # visual shading in ignored region

    # Flash indicators for test taps
    flash_L_until = 0.0
    flash_R_until = 0.0
    def flash(side, now):
        nonlocal flash_L_until, flash_R_until
        if side == "L": flash_L_until = now + 0.20
        else:           flash_R_until = now + 0.20

    # kill (SIGTERM) and a closed terminal (SIGHUP) end the program like Ctrl+C: the finally below
    # then returns the servos to REST. Installed here, in the main thread, before the main loop.
    def _stop_on_signal(signum, frame):
        raise KeyboardInterrupt
    for _name in ("SIGTERM", "SIGHUP"):
        if hasattr(signal, _name):         # SIGHUP does not exist on Windows
            signal.signal(getattr(signal, _name), _stop_on_signal)

    try:
        while True:
            raw = cam.read()
            rect = bot.rect_frame(raw)

            # --- Physical button: same behavior as 'B' key ---
            if button is not None:
                pressed = button.is_pressed  # True while held (to GND)
                if pressed and not prev_button:
                    if mode == MODE_BOT:
                        mode = MODE_HUMAN
                    else:
                        mode = MODE_ARMING
                        arming_until = time.time() + arming_delay_s
                    print(f"[button] mode -> { {0:'HUMAN',1:'ARMING',2:'BOT'}[mode] }")
                prev_button = pressed

            # --- Compute decision line & scan ROI ---
            band_half = 2
            y_dec = int(bot.H * bot.decision_y_frac)
            # ensure ROI covers at least the tripwire band, and extends a margin below the line
            y_scan_max = int(
                min(
                    bot.H,
                    max(y_dec + band_half + 1, int(bot.H * (bot.decision_y_frac + scan_margin_frac)))
                )
            )
            roi = rect[:y_scan_max, :]

            # Masks only in ROI, then placed into full-size arrays
            mg_roi = hsv_mask(roi, bot.good_ranges)
            mb_roi = hsv_mask(roi, bot.bad_ranges)
            mg = np.zeros((bot.H, bot.W), dtype=np.uint8); mg[:y_scan_max, :] = mg_roi
            mb = np.zeros((bot.H, bot.W), dtype=np.uint8); mb[:y_scan_max, :] = mb_roi

            # Compute cutoff (for overlay + optional masking) and remove bottom band
            cutoff_frac = max(bot.decision_y_frac + 0.02, bot.car_y_frac - ignore_band_above_car)
            cutoff_row = int(bot.H * cutoff_frac)
            if ignore_enabled:
                mg[cutoff_row:, :] = 0
                mb[cutoff_row:, :] = 0

            # Clean up masks
            mg = cv2.morphologyEx(mg, cv2.MORPH_OPEN, kernel, iterations=1)
            mb = cv2.morphologyEx(mb, cv2.MORPH_OPEN, kernel, iterations=1)

            # Objects
            good = find_objects(mg, min_area=40)
            bad  = find_objects(mb, min_area=40)

            # Tripwire & game-over timer
            now = time.time()
            y0 = max(0, y_dec - band_half); y1 = min(bot.H, y_dec + band_half + 1)
            mg_band = (mg[y0:y1, :].sum(axis=0) > 0)
            mb_band = (mb[y0:y1, :].sum(axis=0) > 0)
            hit_g = int(mg_band.any()); hit_r = int(mb_band.any())
            if hit_g and now - last_trip_g > 0.15:
                print(f"[trip] GREEN @ t={now:.2f} lane(s): {lane_hits(mg_band, bot.W, bot.lanes)}")
                last_trip_g = now; last_pass_time = now
            if hit_r and now - last_trip_r > 0.15:
                print(f"[trip] RED   @ t={now:.2f} lane(s): {lane_hits(mb_band, bot.W, bot.lanes)}")
                last_trip_r = now; last_pass_time = now

            # Plan (for overlay); execute only in BOT after grace
            plan = bot.plan(good, bad, now)

            if mode == MODE_ARMING:
                if now >= arming_until:
                    bot.tap_side("R")          # logical RIGHT; servo swap handled inside
                    bot.sync_to_game_start()
                    grace_until = now + 1.5
                    last_pass_time = now
                    mode = MODE_BOT
            elif mode == MODE_BOT:
                if now - last_pass_time >= pass_timeout_s:
                    bot.tap_side("R")
                    bot.sync_to_game_start()
                    grace_until = now + 1.5
                    last_pass_time = now
                if now >= grace_until:
                    bot.execute_plan(plan, now)

            # ---- View / overlay ----
            if sanity_view:
                combined = cv2.bitwise_or(mg, mb)
                vis = cv2.bitwise_and(rect, rect, mask=combined)
            else:
                vis = rect.copy()

            if debug_overlay:
                # lane grid & labels
                th = max(2, bot.W // 240)
                for i in range(1, bot.lanes):
                    x = int(i * bot.W / bot.lanes)
                    cv2.line(vis, (x+1, 0), (x+1, bot.H), (0,0,0), th+2, cv2.LINE_AA)
                    cv2.line(vis, (x,   0), (x,   bot.H), (255,255,255), th,   cv2.LINE_AA)
                for i in range(bot.lanes):
                    x0 = int(i * bot.W / bot.lanes); x1 = int((i+1) * bot.W / bot.lanes)
                    cx = (x0 + x1)//2
                    cv2.putText(vis, str(i), (cx-4, 18), cv2.FONT_HERSHEY_SIMPLEX, 0.6, (255,255,255), 2, cv2.LINE_AA)

                # decision line
                cv2.line(vis, (0, y_dec), (bot.W, y_dec), (255,255,255), 2, cv2.LINE_AA)
                # scan limit line
                cv2.line(vis, (0, max(0, y_scan_max-1)), (bot.W, max(0, y_scan_max-1)), (200,180,0), 1, cv2.LINE_AA)

                # nearest objects per lane (tiny tags)
                nearestG = nearest_per_lane(good, bot.W, bot.lanes)
                nearestB = nearest_per_lane(bad,  bot.W, bot.lanes)
                for lane in range(bot.lanes):
                    if nearestG[lane] is not None:
                        cx, cy, _ = nearestG[lane]
                        cy = min(cy, y_dec-2)
                        cv2.putText(vis, "G", (cx-6, cy-6), cv2.FONT_HERSHEY_SIMPLEX, 0.6, (0,255,0), 2, cv2.LINE_AA)
                    if nearestB[lane] is not None:
                        cx, cy, _ = nearestB[lane]
                        cy = min(cy, y_dec-2)
                        cv2.putText(vis, "R", (cx-6, cy-6), cv2.FONT_HERSHEY_SIMPLEX, 0.6, (0,0,255), 2, cv2.LINE_AA)
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

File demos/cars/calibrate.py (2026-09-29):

#!/usr/bin/env python3
# calibrate.py
# Adds decision-line overlay + keyboard/click adjustment, saves decision_y_frac.
"""Calibration tool of the cars demo: writes calibration.json for cars_pca.py.

One OpenCV window shows the camera image (Picamera2, or OpenCV camera 0 when
Picamera2 cannot be started) on the left and the rectified game area on the
right. Space freezes a frame; click the four corners of the game area (the
window asks for TL, TR, BR, BL); Enter rectifies. Then G, B and E, each
followed by a click in the right panel, sample the good (green), bad (red)
and empty colours; Y and a click, or [ and ], set the decision line; S saves
once the corners and all three colours are set.

Usage, on the Raspberry Pi, in the folder where cars_pca.py will run:

    python3 calibrate.py

Needs a display: an OpenCV window with keyboard and mouse. It writes
calibration.json into the current folder. Q or Esc quits. README.md next to
this file lists every key.
"""

import json, time
from datetime import datetime
from pathlib import Path
import cv2, numpy as np

# ---------------- Camera (tiny res + AF) ----------------
class Camera:
    def __init__(self, width=320, height=180):
        self.picam2 = None
        self.cap = None
        self.w, self.h = width, height
        self.fps, self.has_autofocus = None, False
        self.libcamera = None
        self._start_picam2() or self._start_opencv()
        print(f"[cam] {self.backend()} {self.w}x{self.h} @{self.fps or 'unknown'}fps")

    def backend(self): return "Picamera2" if self.picam2 is not None else "OpenCV"

    def _start_picam2(self):
        try:
            from picamera2 import Picamera2
            import libcamera
            self.libcamera = libcamera
            self.picam2 = Picamera2()
            for f in (120, 90, 60, 30):
                try:
                    cfg = self.picam2.create_video_configuration(
                        main={"size": (self.w, self.h), "format": "RGB888"},
                        controls={"FrameDurationLimits": (int(1e6/f), int(1e6/f))}
                    )
                    self.picam2.configure(cfg); self.picam2.start(); time.sleep(0.2); self.fps = f; break
                except Exception:
                    try: self.picam2.stop()
                    except Exception: pass
                    self.picam2 = Picamera2()
            try:
                self.picam2.set_controls({"AfMode": self.libcamera.controls.AfModeEnum.Continuous})
                self.has_autofocus = True; print("[cam] Picamera2 AF: Continuous")
            except Exception: pass
            return True
        except Exception as e:
            print(f"[cam] Picamera2 not available ({e})"); self.picam2 = None; return False

    def _start_opencv(self):
        self.cap = cv2.VideoCapture(0)
        if not self.cap.isOpened(): raise RuntimeError("No camera")
        self.cap.set(cv2.CAP_PROP_FRAME_WIDTH, self.w);  self.cap.set(cv2.CAP_PROP_FRAME_HEIGHT, self.h)
        for f in (120, 90, 60, 30):
            if self.cap.set(cv2.CAP_PROP_FPS, f): self.fps = f; break
        try:
            if hasattr(cv2, "CAP_PROP_AUTOFOCUS"):
                self.cap.set(cv2.CAP_PROP_AUTOFOCUS, 1); self.has_autofocus = True; print("[cam] UVC AF: requested")
        except Exception: pass

    def read_raw(self):
        if self.picam2 is not None:
            rgb = self.picam2.capture_array()
            return cv2.cvtColor(rgb, cv2.COLOR_RGB2BGR)
        ok, frame = self.cap.read()
        if not ok: raise RuntimeError("Capture failed")
        return frame

    def refocus(self):
        if self.picam2 is not None and self.has_autofocus:
            try: self.picam2.set_controls({"AfTrigger": self.libcamera.controls.AfTrigger.Start}); print("[cam] AF trigger")
            except Exception: pass
        elif self.cap is not None and self.has_autofocus:
            try: self.cap.set(cv2.CAP_PROP_AUTOFOCUS, 0); time.sleep(0.05); self.cap.set(cv2.CAP_PROP_AUTOFOCUS, 1); print("[cam] AF toggle")
            except Exception: pass

    def reconfigure(self, width, height):
        self.w, self.h = width, height
        if self.picam2 is not None:
            from picamera2 import Picamera2
            try: self.picam2.stop()
            except Exception: pass
            self.picam2 = Picamera2(); self._start_picam2()
        else:
            self.cap.release(); self._start_opencv()
        print(f"[cam] Reconfigured {self.backend()} {self.w}x{self.h} @{self.fps or 'unknown'}fps")

    def release(self):
        if self.picam2 is not None:
            try: self.picam2.stop()
            except Exception: pass
        if self.cap is not None: self.cap.release()

# ---------------- Helpers ----------------
def overlay_text(img, lines, y0=24):
    y = y0
    for ln in lines:
        cv2.putText(img, ln, (10, y), cv2.FONT_HERSHEY_SIMPLEX, 0.6, (255,255,255), 2, cv2.LINE_AA); y += 22

def draw_points(img, pts, color=(0,255,255)):
    for (x,y) in pts: cv2.circle(img, (int(x),int(y)), 5, color, 2)

def median_patch_hsv(bgr, cx, cy, r=6):
    h,w = bgr.shape[:2]; x0,x1 = max(0,cx-r), min(w,cx+r+1); y0,y1 = max(0,cy-r), min(h,cy+r+1)
    hsv = cv2.cvtColor(bgr[y0:y1, x0:x1], cv2.COLOR_BGR2HSV); med = np.median(hsv.reshape(-1,3), axis=0)
    return med.astype(np.uint8)

def hsv_ranges_around(center_hsv, dH=12, dS=70, dV=70):
    h,s,v = map(int, center_hsv); loS,hiS = max(0,s-dS),min(255,s+dS); loV,hiV = max(0,v-dV),min(255,v+dV)
    loH,hiH = h-dH, h+dH
    if loH < 0:
        return [([0,loS,loV],[hiH%180,hiS,hiV]), ([180+loH,loS,loV],[179,hiS,hiV])]
    if hiH > 179:
        return [([0,loS,loV],[hiH-180,hiS,hiV]), ([loH,loS,loV],[179,hiS,hiV])]
    return [([loH,loS,loV],[hiH,hiS,hiV])]

def warp_perspective(img, corners_src, dst_size):
    W,H = dst_size; dst = np.float32([[0,0],[W-1,0],[W-1,H-1],[0,H-1]])
    M = cv2.getPerspectiveTransform(np.float32(corners_src), dst)
    return M, cv2.warpPerspective(img, M, (W,H))

def order_quad(pts):
    pts = np.array(pts, dtype=np.float32)
    s = pts.sum(axis=1); d = np.diff(pts, axis=1).reshape(-1)
    ordered = np.zeros((4,2), np.float32)
    ordered[0] = pts[np.argmin(s)]   # TL
    ordered[2] = pts[np.argmax(s)]   # BR
    ordered[1] = pts[np.argmin(d)]   # TR
    ordered[3] = pts[np.argmax(d)]   # BL
    return ordered
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

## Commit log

2025-08-11 Initial release
    [actuator_arm_base_motor_holder.ipt, actuator_arm_base_motor_holder.stl, actuator_arm_base_motor_holder_single_hole.ipt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]
2026-02-10 Add PCA servo demo
